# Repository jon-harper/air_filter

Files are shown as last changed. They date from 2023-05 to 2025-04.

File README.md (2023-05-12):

# SUAFT: Still Unnamed Air Filter Thing

3D printer air filtration with HEPA and activated carbon.

## Overview

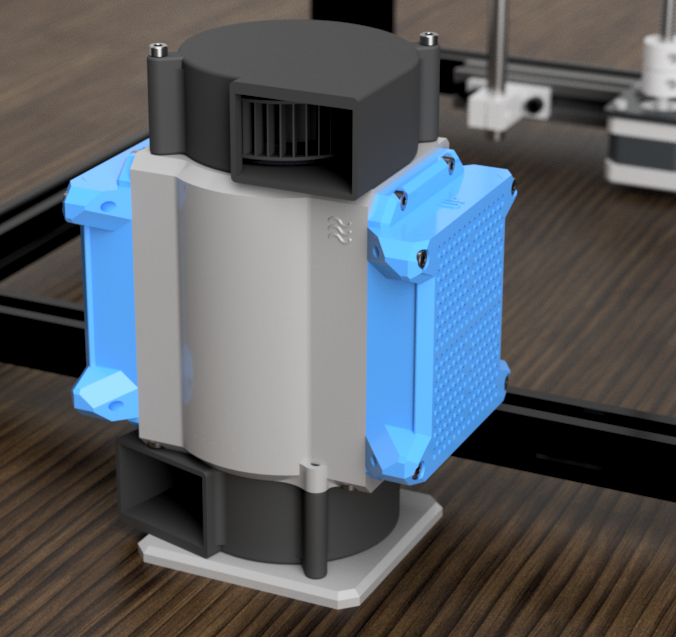
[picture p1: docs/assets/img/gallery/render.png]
render


This is a combination activated carbon and HEPA filter for 3D printing. It uses 75x30mm fans (either one or two) to draw air through a wall of activated carbon pellets and then through a HEPA filter.

The filter can be printed with one fan for filtration only, or with a second fan to provide chamber exhaust or additional airflow.

A method of mounting the filter to 2020 extrusions is coming soon.

[Documentation](https://jon-harper.github.io/air_filter/) is available.

## Bill of Materials
* [Single Filter](https://jon-harper.github.io/air_filter/single/)
* [Dual Filter](https://jon-harper.github.io/air_filter/dual/)

## Assembly
* [Heat Set Insert Locations](https://jon-harper.github.io/air_filter/inserts/)
* [Assembly Guide](https://jon-harper.github.io/air_filter/assembly/)

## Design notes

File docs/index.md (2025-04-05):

---
title: Still Unnamed Air Filter Thing
summary: Landing page for the Still Unnamed Air Filter Thing
authors: Jon Harper
date: 2024-7-31
hide: toc
---

# [SUAFT 120](v3/index.md)

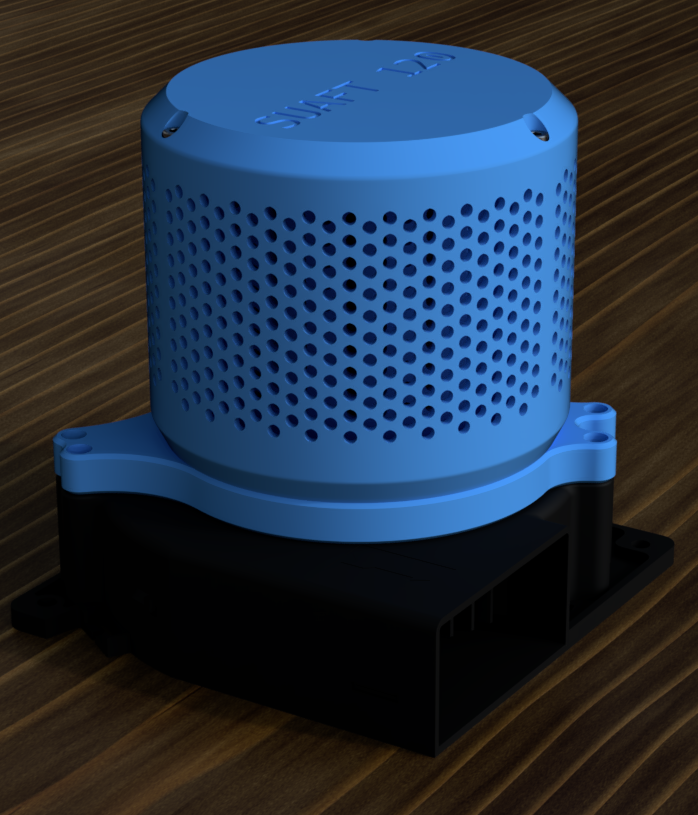
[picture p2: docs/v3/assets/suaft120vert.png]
SUAFT 120


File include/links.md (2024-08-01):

[bom_7530_fan]: https://www.amazon.com/dp/B08NCMY3H5
[bom_hepa]: https://www.amazon.com/gp/product/B08JPDWQCL
[bom_inserts]: https://www.amazon.com/uxcell-Knurled-Insert-Female-Embedding/dp/B09MCWTBCC
[bom_tubing]: https://www.amazon.com/DMiotech-Silicone-Translucent-Industrial-Tubing/dp/B0B59F8WCW
[bom_carbon]: https://www.amazon.com/dp/B00XIIDB8Y/
[bom_magnet]: https://www.amazon.com/TRYMAG-Magnets-Refrigerator-Whiteboard-Neodymium/dp/B09QHSB2XM/

[stl_main_body]:  https://github.com/jon-harper/air_filter/blob/main/STL/V1/main_body.stl
[stl_exhaust_coupler]: https://github.com/jon-harper/air_filter/blob/main/STL/V1/exhaust_coupler.stl
[stl_fan_base]:   https://github.com/jon-harper/air_filter/blob/main/STL/V1/fan_base.stl
[stl_fan_cap]:    https://github.com/jon-harper/air_filter/blob/main/STL/V1/fan_cap.stl
[stl_simple_cap]: https://github.com/jon-harper/air_filter/blob/main/STL/V1/simple_cap.stl
[stl_filter_base]:    https://github.com/jon-harper/air_filter/blob/main/STL/V1/ac_filter/filter_base.stl
[stl_filter_cover]:   https://github.com/jon-harper/air_filter/blob/main/STL/V1/ac_filter/filter_cover.stl
[stl_cpap_coupler]: https://github.com/jon-harper/air_filter/blob/main/STL/V1/15mm_cpap_coupler.stl

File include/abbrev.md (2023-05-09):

*[SHCS]: socket head cap screw
*[AC]: activated carbon
*[HEPA]: high efficiency particulate air

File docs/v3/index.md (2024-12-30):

---
title: SUAFT 120 Introduction
summary: Overview of the 120mm version of SUAFT.
authors: Jon Harper
date: 2024-12-8
hide: toc
---

<div markdown class="jh-grid-container jh-grid-2">
<div markdown class="jh-card">

SUAFT 120 is an activated carbon and HEPA filter for 3D printer enclosures. SUAFTs are designed to be simple, cheap, and efficient; v3 builds on v1 with a sleeker design and easier disassembly.

## Goals

1. Be simple and efficient.
2. Be easy to build.
3. Be cheap to source.
</div>
<div markdown class="jh-grid-img">
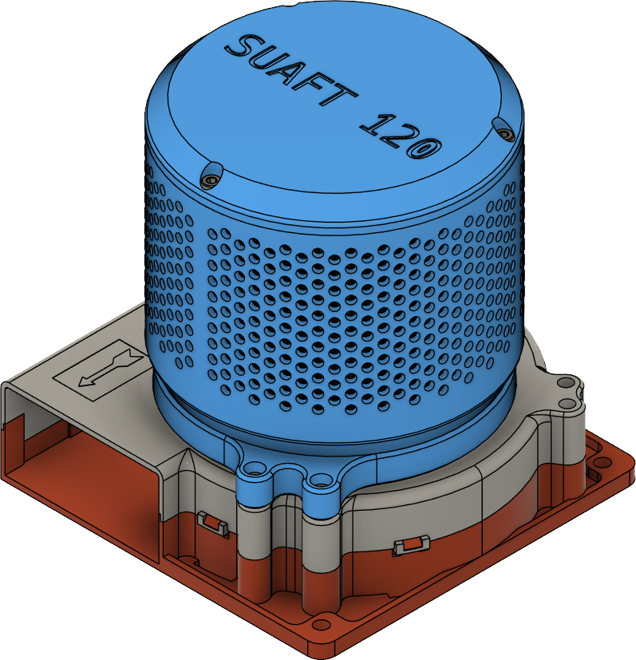
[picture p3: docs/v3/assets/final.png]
SUAFT

</div>
</div>

## Bill of Materials

The filter can be printed for single or dual fan operation. A single fan should be used for continuous filtration. Dual fans can be used for large format printers or as an exhaust filter.

[SUAFT 120 Bill of Materials](bom.md){ .md-button }

## Materials

Material choice is guided by enclosure operating temperature.

- CF-ASA, CF-ABS: >80C, <95C
- ASA: >60C
- ABS: >45C. Avoid with active heaters.
- PETG: <45C or chamber floor. PETG filters should be considered a temporary solution (expected to fail with time). Do not use with active heaters.

## Assembly
 
[Preparation](prep.md){ .md-button }

[Assembly](assembly.md){ .md-button }

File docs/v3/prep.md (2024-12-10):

---
title: Preparation
summary: Simple assembly overview
authors: Jon Harper
date: 2024-12-8
---

## Heat Set Inserts

<figure markdown>
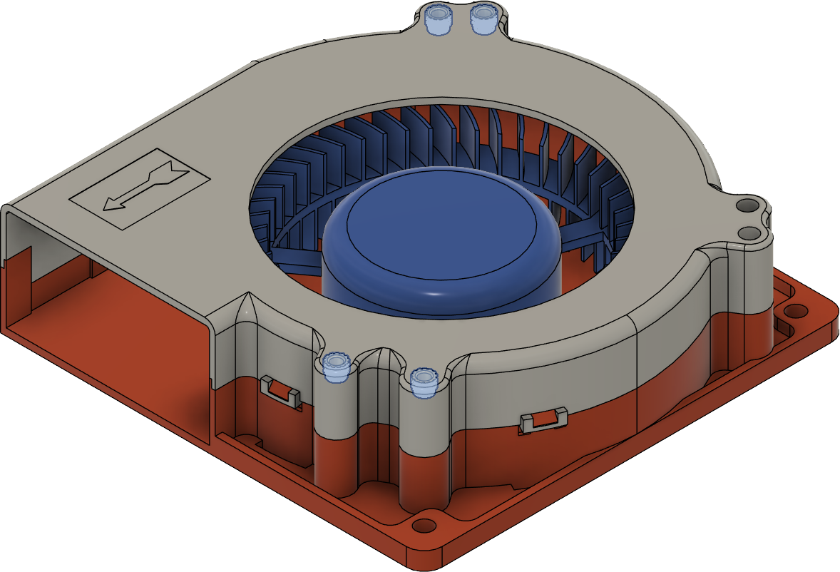
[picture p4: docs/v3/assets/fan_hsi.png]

<figcaption markdown>
Step 1. Install heat set inserts into three (3) of the four (4) highlighted holes in the fan. The fourth may be left unused.
</figcaption>
</figure>

<figure markdown>
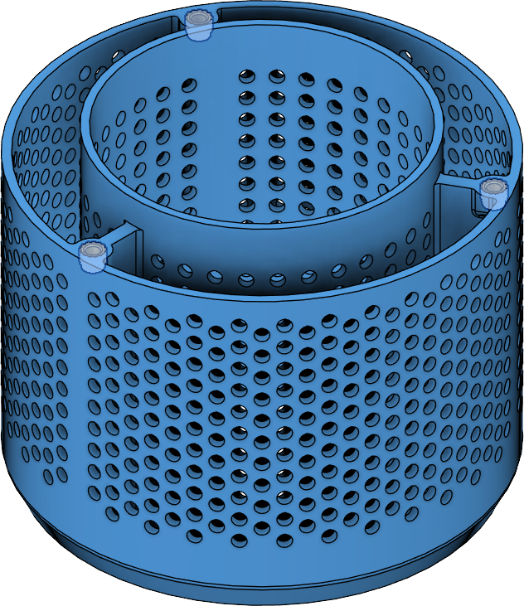
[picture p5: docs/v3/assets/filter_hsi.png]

<figcaption markdown>
Step 2. Install heat set inserts into the three (3) highlighted holes in the fitler cage.
</figcaption>
</figure>

## Magnet Installation

<figure markdown>
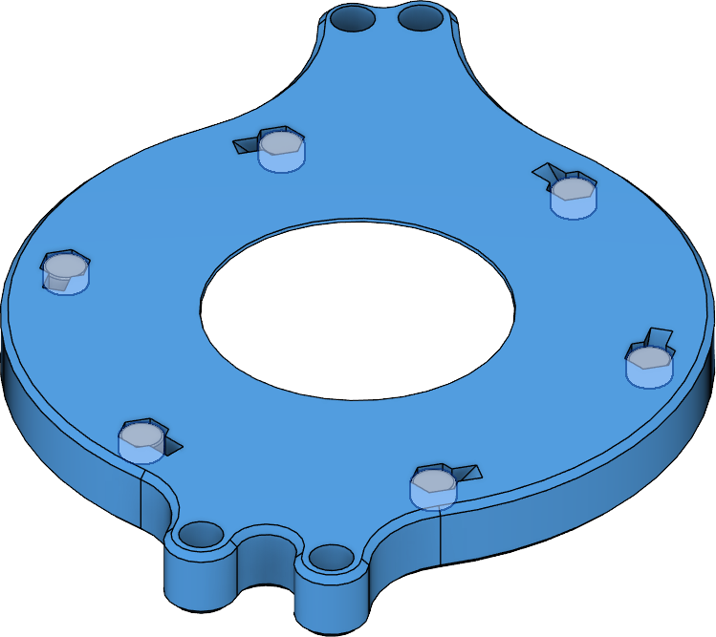
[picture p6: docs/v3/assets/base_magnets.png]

<figcaption markdown>
Step 1. Fix magnets into the six (6) highlighted locations. **It is strongly recommended that the polarity of the magnets are all oriented the same direction.**
</figcaption>
</figure>

<figure markdown>
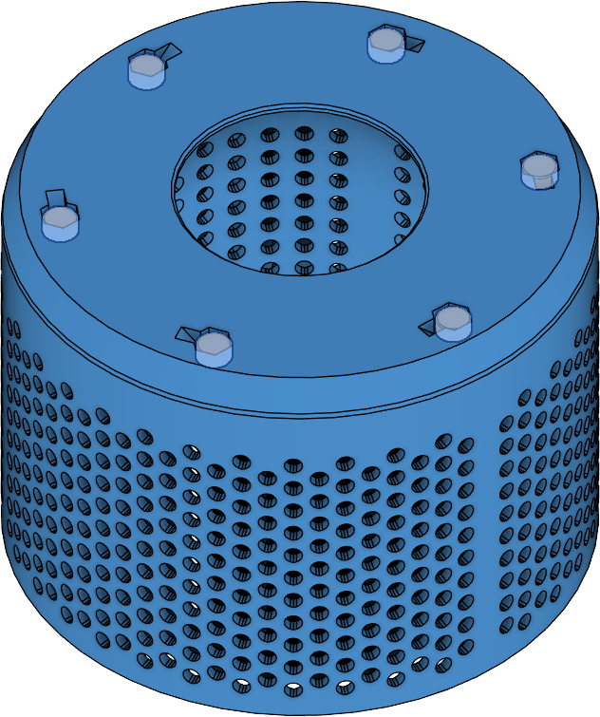
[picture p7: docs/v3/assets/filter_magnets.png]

<figcaption markdown>
Step 2. Fix magnets into the six (6) highlighted locations. **These magnets must have the same orientation as the base magnets.**
</figcaption>
</figure>

<figure markdown>
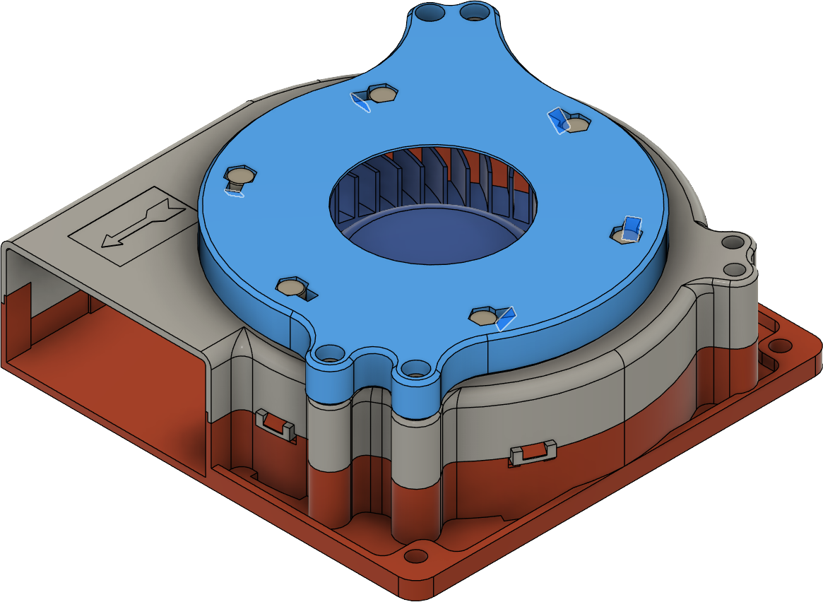
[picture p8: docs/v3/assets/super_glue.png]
step 3

<figcaption markdown>
Step 3. Test that the filter and base snap together properly. Once any issues are fixed, optionally add a drop of super glue to the highlighted well area next to each magnet; this will help ensure magnets do not come loose.
</figcaption>
</figure>

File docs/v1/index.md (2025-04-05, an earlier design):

---
title: v1 Introduction
summary: Landing page for the Still Unnamed Air Filter Thing
authors: Jon Harper
date: 2023-5-5
hide: toc
---

!!! caution
    This project is deprecated. Visit [SUAFT 120](../v3) for the latest design.

<div markdown class="jh-grid-container jh-grid-2">
<div markdown class="jh-card">

SUAFT is an activated carbon and HEPA filter for 3D printer enclosures.

## Goals

1. Be simple and efficient.
2. Be easy to build.
3. Be cheap to source.
</div>
<div markdown class="jh-grid-img">
SUAFT
</div>
</div>
## Bill of Materials

The filter can be printed with either one or two fans. The second fan can be used to provide additional airflow or act as a controlled chamber exhaust fan.

A method of mounting the filter to 2020 extrusions is coming soon.

[Single Fan BOM](single.md){ .md-button }

[Dual Fan BOM](dual.md){ .md-button }

## Assembly

Print SUAFT with ASA, ABS, or PETG. If your enclosure regularly reaches 60C, ASA is recommended.

[Heat Set Insert Locations](inserts.md){ .md-button }

[Assembly Guide](assembly.md){ .md-button }

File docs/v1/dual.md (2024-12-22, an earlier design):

---
title: Dual Fan BOM
summary: Information on the dual fan variation.
authors: Jon Harper
date: 2023-5-7
hide: toc
---

## Materials

| Part | Qty |
|---|-----|
| [Radial 75mm x 30mm fan][bom_7530_fan] | 2 ea |
| [Moosoo XL-618A HEPA Filter][bom_hepa] | 1 ea |
| M3 x 35mm SHCS | 4 ea |
| M3 x 6mm SHCS | 20 ea |
| [Heat set inserts, M3 x 5mm x 4mm][bom_inserts] | 24 ea |
| [Acid-free coconut shell activated carbon][bom_carbon] | < 0.5kg/1lb |
| :material-printer-3d-nozzle: [`main_body.stl`][stl_main_body] | 1 ea |
| :material-printer-3d-nozzle: [`fan_cap.stl`][stl_fan_cap] | 1 ea |
| :material-printer-3d-nozzle: [`fan_base.stl`][stl_fan_base] | 1 ea |
| :material-printer-3d-nozzle: [`filter_base.stl`][stl_filter_base] | 2 ea |
| :material-printer-3d-nozzle: [`filter_cover.stl`][stl_filter_cover] | 2 ea |

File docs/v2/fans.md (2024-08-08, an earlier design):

---
title: 2. Fan Cage(s)
summary: Assembling fan cages
authors: Jon Harper
date: 2024-7-31
---

## Left Fan Cage

<figure markdown>
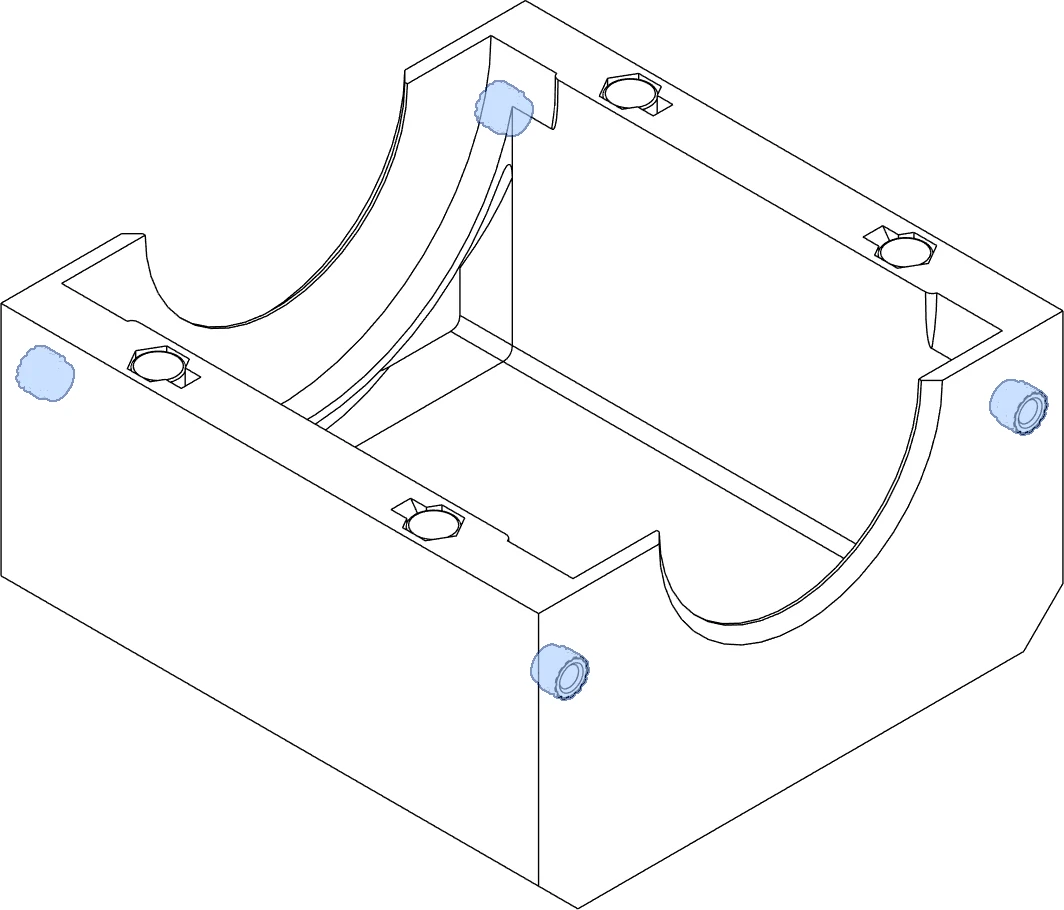
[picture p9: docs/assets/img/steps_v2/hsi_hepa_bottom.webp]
step 1

<figcaption markdown>
Step 1. 
</figcaption>
</figure>

## Right Fan Cage

!!! note
    If your build does not use a second fan, jump to the next section.

<figure markdown>
step 1
<figcaption markdown>
Step 1. 
</figcaption>
</figure>

## Filter Cap

!!! note
    If your build has two (2) fans, skip this section.

<figure markdown>
step 1
<figcaption markdown>
Step 1. 
</figcaption>
</figure>

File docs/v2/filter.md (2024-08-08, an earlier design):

---
title: 3. Filter Assembly
summary: Assembling the filter
authors: Jon Harper
date: 2024-7-31
---

## AC Filter

## HEPA Filter

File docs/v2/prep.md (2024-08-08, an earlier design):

---
title: 1. Prep
summary: Simple assembly overview
authors: Jon Harper
date: 2024-7-31
---

## Heat Set Inserts

<figure markdown>
step 1
<figcaption markdown>
Step 1. 
</figcaption>
</figure>

<figure markdown>
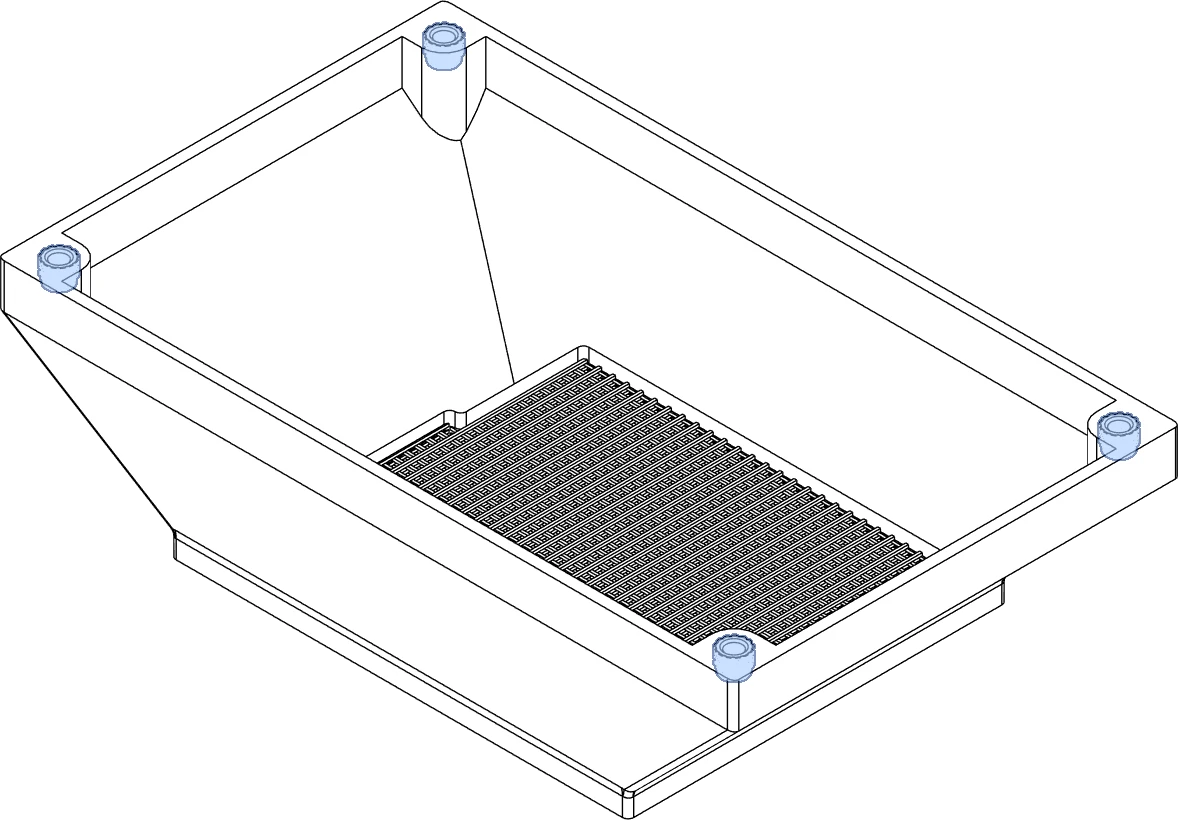
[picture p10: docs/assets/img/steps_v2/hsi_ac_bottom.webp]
step 2

<figcaption markdown>
Step 2. 
</figcaption>
</figure>

<figure markdown>
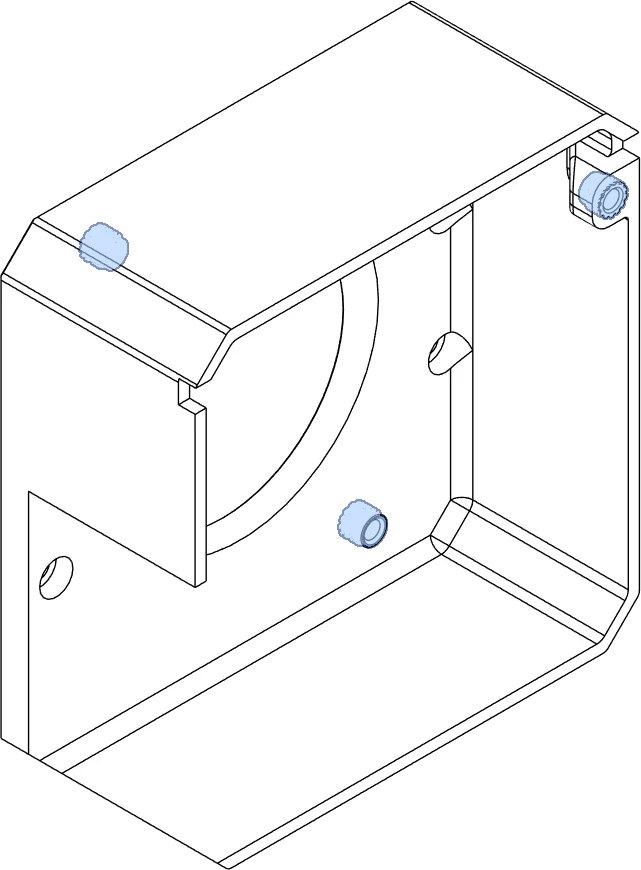
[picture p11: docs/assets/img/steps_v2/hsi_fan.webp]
step 3

<figcaption markdown>
Step 3. 
</figcaption>
</figure>

## Magnet Installation

<figure markdown>
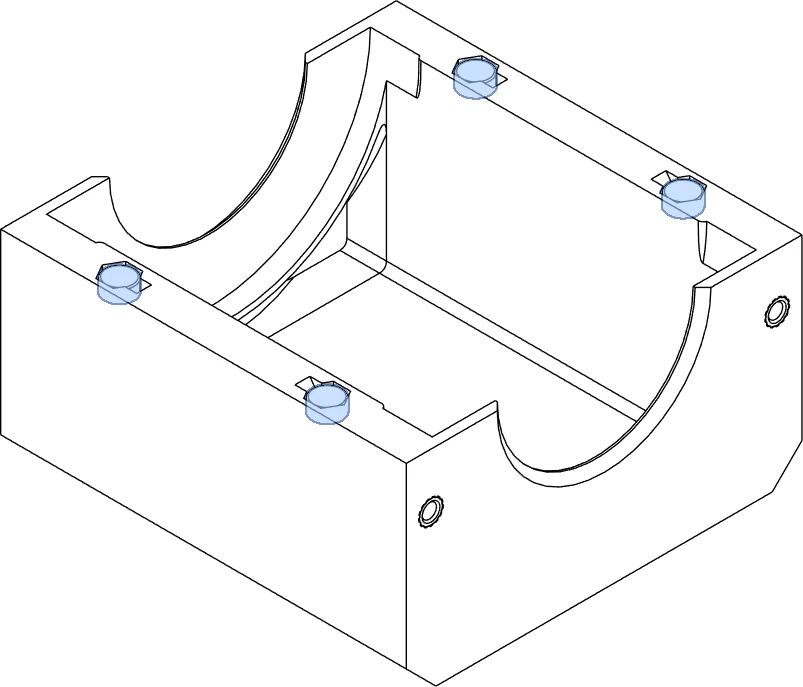
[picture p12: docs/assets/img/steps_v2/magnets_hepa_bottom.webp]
step 1

<figcaption markdown>
Step 1. 
</figcaption>
</figure>

<figure markdown>
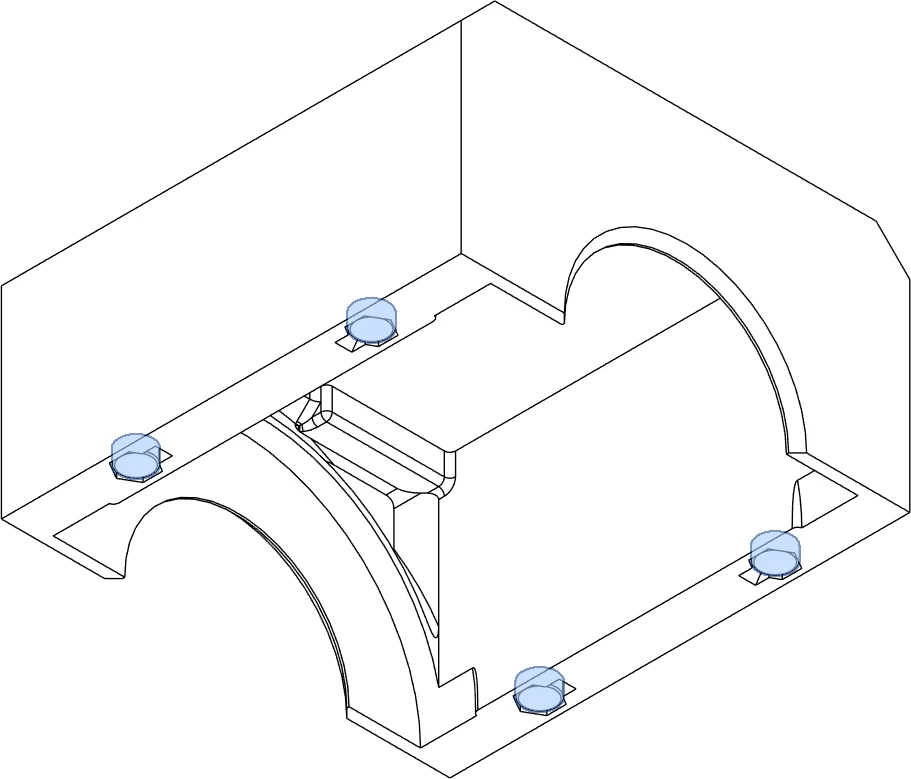
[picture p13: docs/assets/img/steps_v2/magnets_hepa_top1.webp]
step 2

<figcaption markdown>
Step 2. 
</figcaption>
</figure>

<figure markdown>
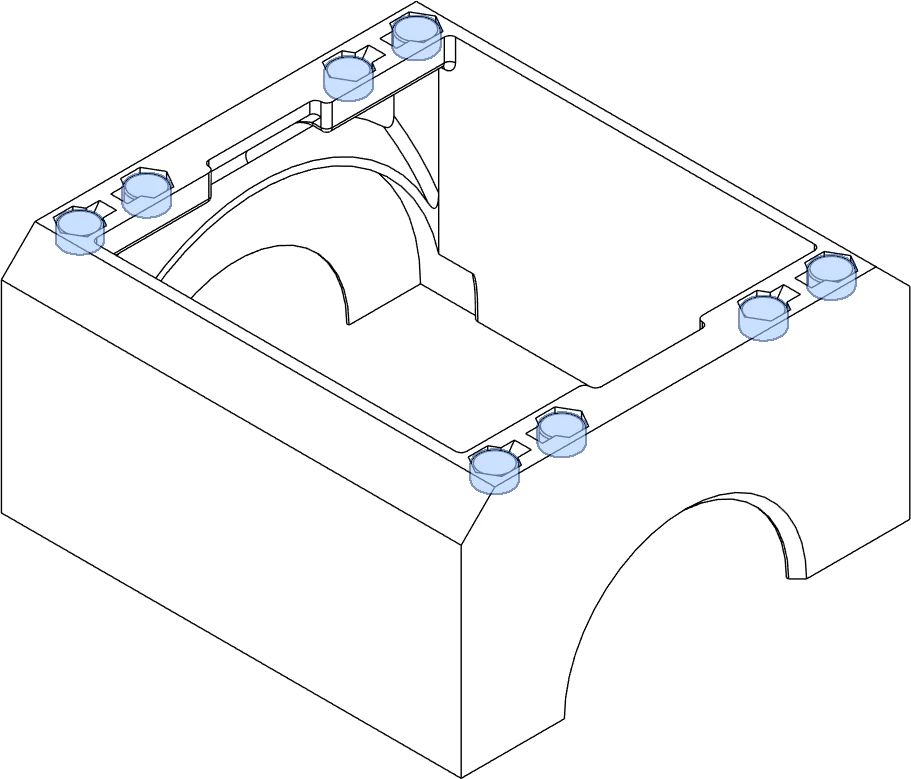
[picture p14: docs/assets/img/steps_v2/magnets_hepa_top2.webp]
step 3

<figcaption markdown>
Step 3. 
</figcaption>
</figure>

<figure markdown>
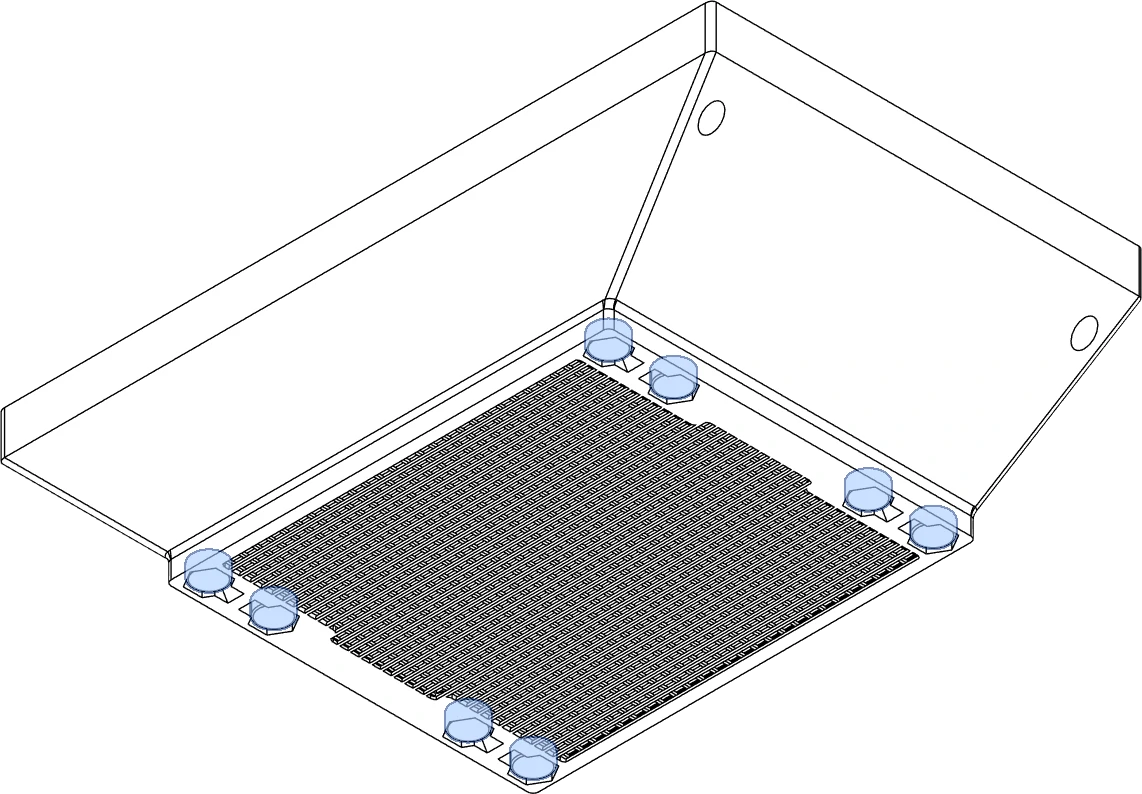
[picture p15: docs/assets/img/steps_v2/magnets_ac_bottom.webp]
step 4

<figcaption markdown>
Step 4. 
</figcaption>
</figure>

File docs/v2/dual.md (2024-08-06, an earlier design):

---
title: Dual Fan BOM
summary: Information on the dual fan variation.
authors: Jon Harper
date: 2024-7-31
hide: toc
---

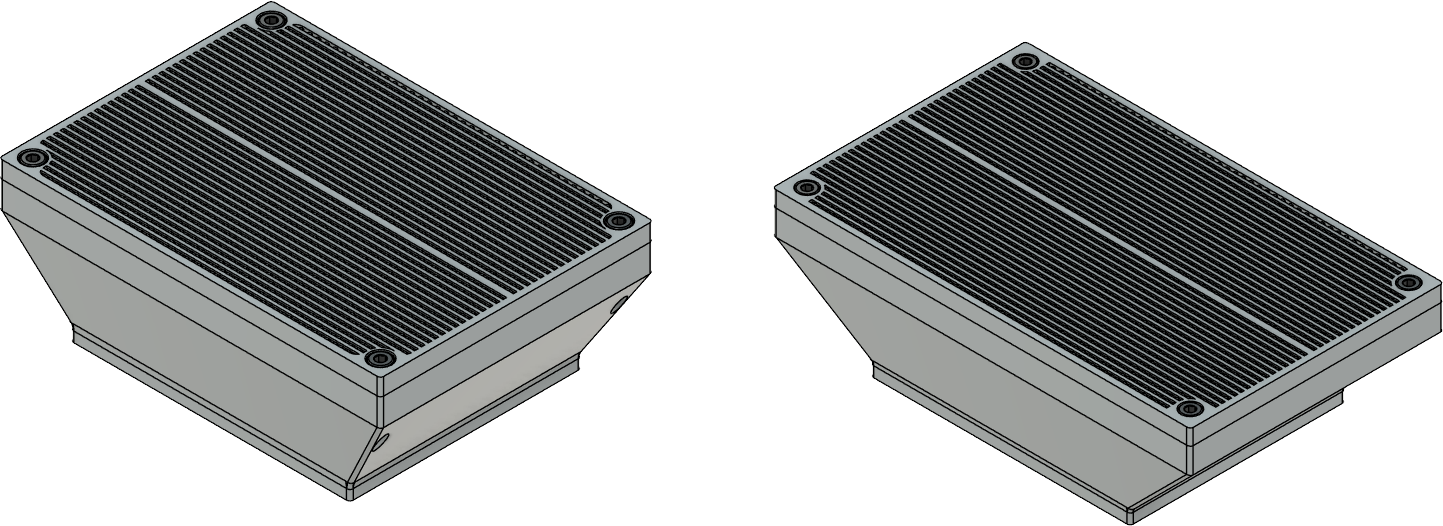
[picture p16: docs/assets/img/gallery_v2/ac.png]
preview


## Materials

| Part | Qty |
|---|-----|
| [Radial 75mm x 30mm fan][bom_7530_fan] | 2 ea |
| [Moosoo XL-618A HEPA Filter][bom_hepa] | 1 ea |
| M3 x 35mm SHCS | 4 ea |
| M3 x 6mm SHCS | 10 ea |
| [6mm x 3mm magnets][bom_magnet] | 24 |
| [Heat set inserts, M3 x 5mm x 4mm][bom_inserts] | 14 ea |
| [Acid-free coconut shell activated carbon][bom_carbon] | < 0.5kg/1lb |
| :material-printer-3d-nozzle: [`HEPA Top.stl`][v2_hepa_top] | 1 ea |
| :material-printer-3d-nozzle: [`HEPA Bottom.stl`][v2_bottom] | 1 ea |
| :material-printer-3d-nozzle: [`Fan Base.stl`][v2_fan_lid] | 2 ea |
| :material-printer-3d-nozzle: [`Fan Lid.stl`][v2_ac_lid_solo] | 2 ea |
| :material-printer-3d-nozzle: [`AC Base - Solo.stl`][v2_ac_base_solo] | 1 ea |
| :material-printer-3d-nozzle: [`AC Lid - Solo.stl`][v2_ac_lid_solo] | 1 ea |

[v2_coupler]: https://github.com/jon-harper/air_filter/blob/main/STL/V2/Fan%20Cages/15mm%20CPAP%20Coupler.stl
[v2_ac_base_duo]: https://github.com/jon-harper/air_filter/blob/main/STL/V2/AC%20Filter/AC%20Base%20-%20Duo.stl
[v2_ac_base_solo]: https://github.com/jon-harper/air_filter/blob/main/STL/V2/AC%20Filter/AC%20Base%20-%20Solo.stl
[v2_ac_lid_duo]: https://github.com/jon-harper/air_filter/blob/main/STL/V2/AC%20Filter/AC%20Lid%20-%20Duo.stl
[v2_ac_lid_solo]: https://github.com/jon-harper/air_filter/blob/main/STL/V2/AC%20Filter/AC%20Lid%20-%20Solo.stl
[v2_fan_base]: https://github.com/jon-harper/air_filter/blob/main/STL/V2/Fan%20Cages/Fan%20Base.stl
[v2_fan_lid]: https://github.com/jon-harper/air_filter/blob/main/STL/V2/Fan%20Cages/Fan%20Lid.stl
[v2_filter_cap]: https://github.com/jon-harper/air_filter/blob/main/STL/V2/Fan%20Cages/Filter%20Cap.stl
[v2_hepa_top]: https://github.com/jon-harper/air_filter/blob/main/STL/V2/HEPA/HEPA%20Top.stl
[v2_bottom]: https://github.com/jon-harper/air_filter/blob/main/STL/V2/HEPA/HEPA%20Bottom.stl
[v2_bottom_wago]: https://github.com/jon-harper/air_filter/blob/main/STL/V2/HEPA/HEPA%20Bottom%20-%20Wagos.stl
[v2_bottom_2020]: https://github.com/jon-harper/air_filter/blob/main/STL/V2/HEPA/HEPA%20Bottom%20-%202020%20Mount.stl
[v2_bottom_2020_splitter]: https://github.com/jon-harper/air_filter/blob/main/STL/V2/HEPA/HEPA%20Bottom%20-%202020%20Mount%20with%20Splitter.stl
[v2_bottom_2020_wago]: https://github.com/jon-harper/air_filter/blob/main/STL/V2/HEPA/HEPA%20Bottom%20-%202020%20Mount%20with%20Wagos.stl

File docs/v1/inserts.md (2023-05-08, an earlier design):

---
title: Heat Set Inserts
summary: Locations of heat set inserts
authors: Jon Harper
date: 2023-5-7
# hide: toc
---

## main_body.stl

<div markdown class="jh-grid-container jh-grid-2">
<div markdown class="jh-grid-img">
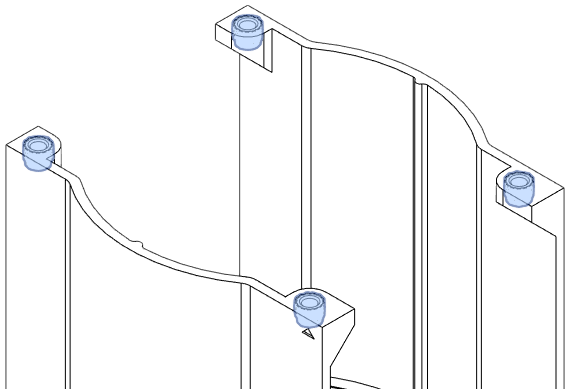
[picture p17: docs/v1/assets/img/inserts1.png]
top inserts

</div>
<div markdown class="jh-grid-img">
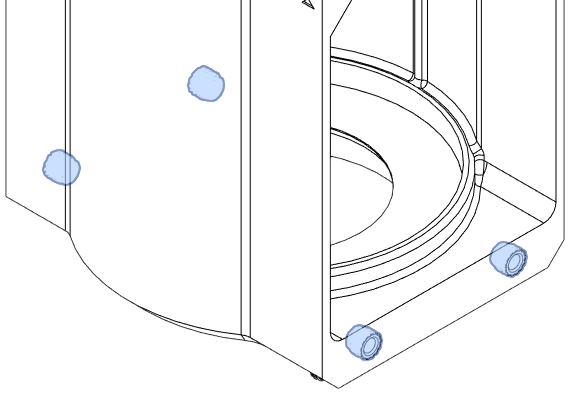
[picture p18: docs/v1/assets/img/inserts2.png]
base inserts

</div>
<div markdown class="jh-grid-img">
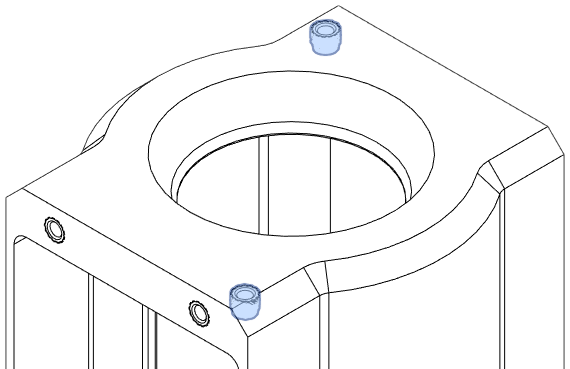
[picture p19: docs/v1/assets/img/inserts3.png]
fan inserts

</div>
</div>

## fan_cap.stl

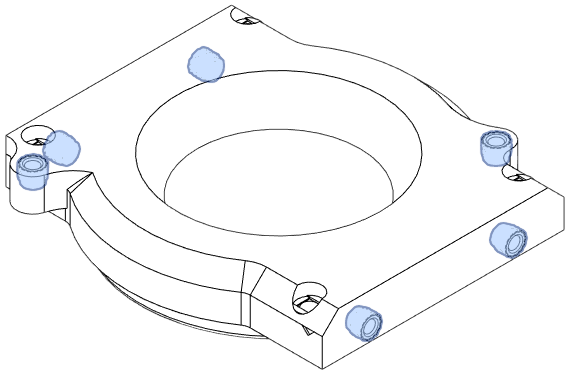
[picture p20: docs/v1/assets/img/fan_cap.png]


## filter_base.stl

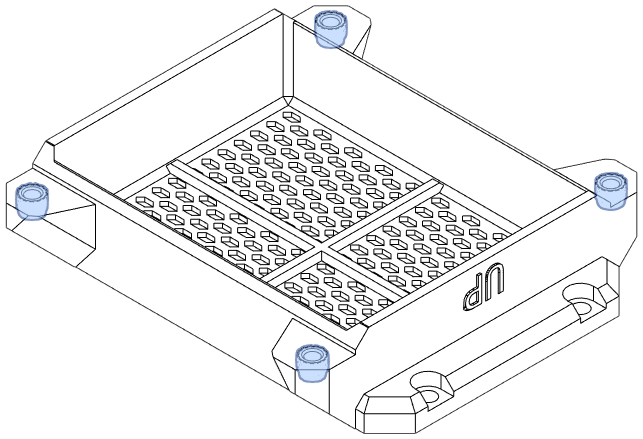
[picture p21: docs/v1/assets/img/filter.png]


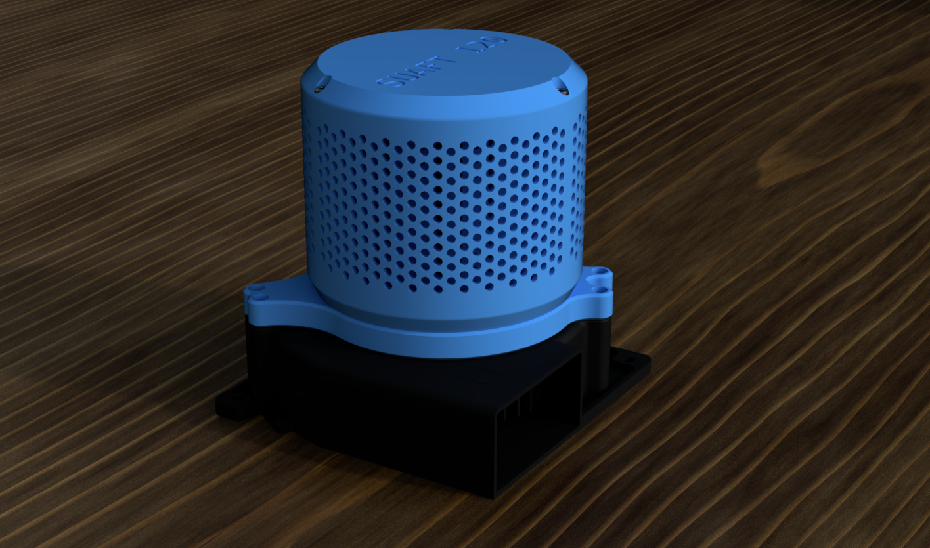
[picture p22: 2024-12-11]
docs/v3/assets/suaft120.png

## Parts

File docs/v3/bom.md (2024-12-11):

---
title: Bill of Materials
summary: Information on the dual fan variation.
authors: Jon Harper
date: 2024-12-8
hide: toc
---

## Materials

| Part | Qty |
|---|-----|
| [Radial 120mm x 32mm fan][bom_120_fan] | 1 ea |
| [Moosoo XL-618A HEPA Filter][bom_hepa] | 1 ea |
| M3 x 6mm SHCS | 6 ea |
| [6mm x 3mm magnets][bom_magnet] | 12 |
| [Heat set inserts, M3 x 5mm x 4mm][bom_inserts] | 6 ea |
| [Acid-free coconut shell activated carbon][bom_carbon] | < 0.5kg/1lb |
| :material-printer-3d-nozzle: [`Base.stl`][120_base] | 1 ea |
| :material-printer-3d-nozzle: [`Filter Cap.stl`][120_filter_cap] | 1 ea |
| :material-printer-3d-nozzle: [`Filter.stl`][120_filter] | 1 ea |
| :material-printer-3d-nozzle: [`Funnel.stl`][120_funnel] | 1 ea, Optional |

[120_base]: https://github.com/jon-harper/air_filter/blob/main/STL/120/Base.stl
[120_filter_cap]: https://github.com/jon-harper/air_filter/blob/main/STL/120/Filter%20Cap.stl
[120_filter]: https://github.com/jon-harper/air_filter/blob/main/STL/120/Filter.stl
[120_funnel]: https://github.com/jon-harper/air_filter/blob/main/STL/120/Funnel.stl
[bom_120_fan]: https://www.amazon.com/Wathai-Brushless-Cooling-Centrifugal-Airflow/dp/B07RMJC9NT/

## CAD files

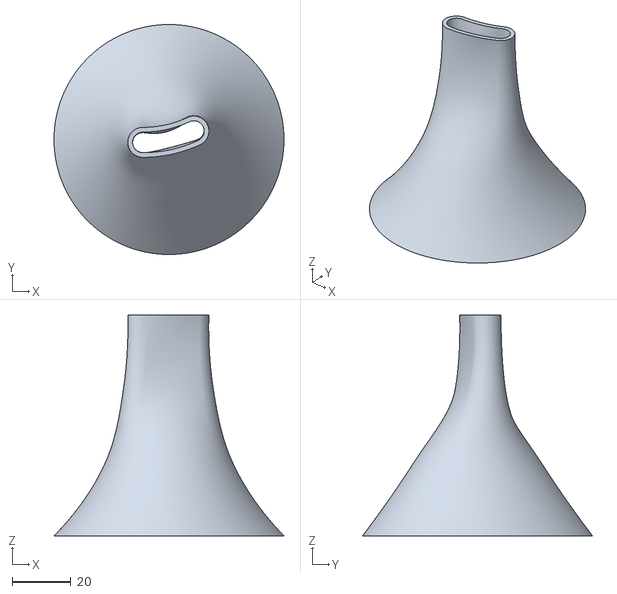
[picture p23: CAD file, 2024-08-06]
STL/120/Funnel.stl
78.2 x 78.2 x 75.0

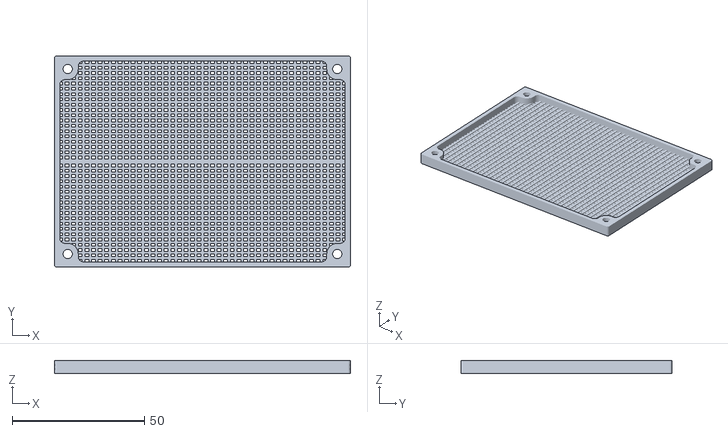
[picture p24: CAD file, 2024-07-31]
STL/V2/AC Filter/AC Lid - Solo.stl
112.0 x 80.0 x 5.00

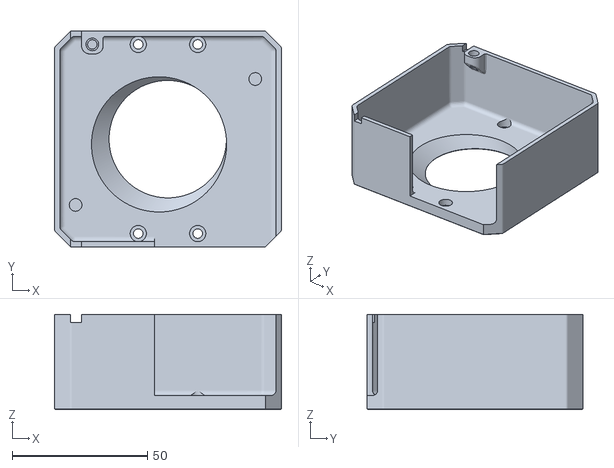
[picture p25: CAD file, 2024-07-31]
STL/V2/Fan Cages/Fan Base.stl
84.0 x 80.0 x 35.2

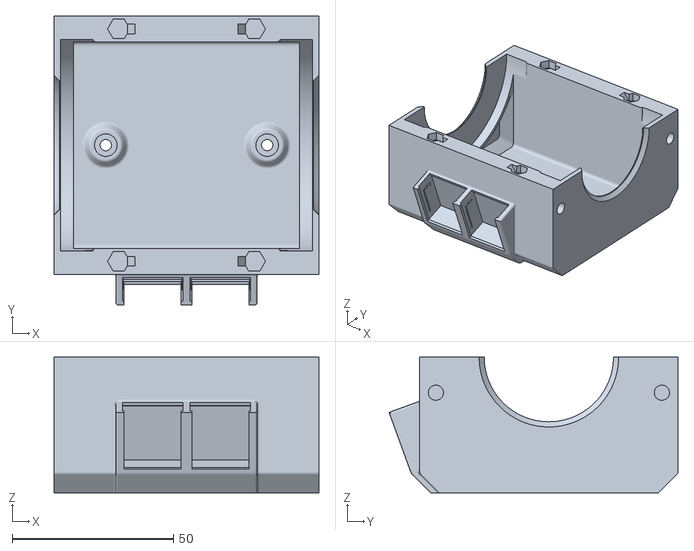
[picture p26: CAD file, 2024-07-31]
STL/V2/HEPA/HEPA Bottom - 2020 Mount with Wagos.stl
82.0 x 89.5 x 42.0

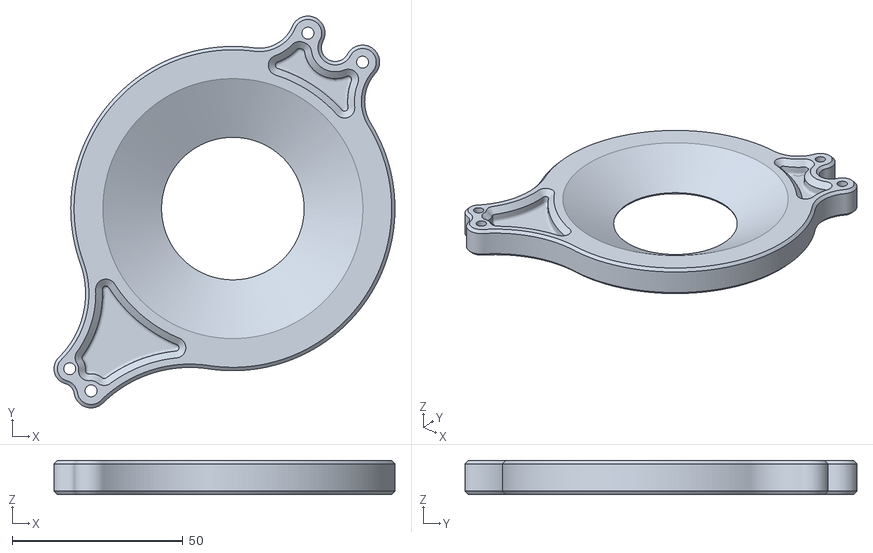
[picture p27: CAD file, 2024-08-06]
STL/120/Base.stl
99.9 x 114.8 x 10.0

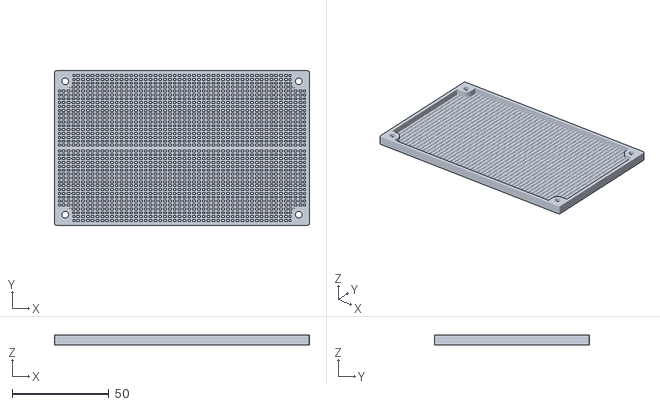
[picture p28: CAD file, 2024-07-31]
STL/V2/AC Filter/AC Lid - Duo.stl
132.0 x 80.0 x 5.00

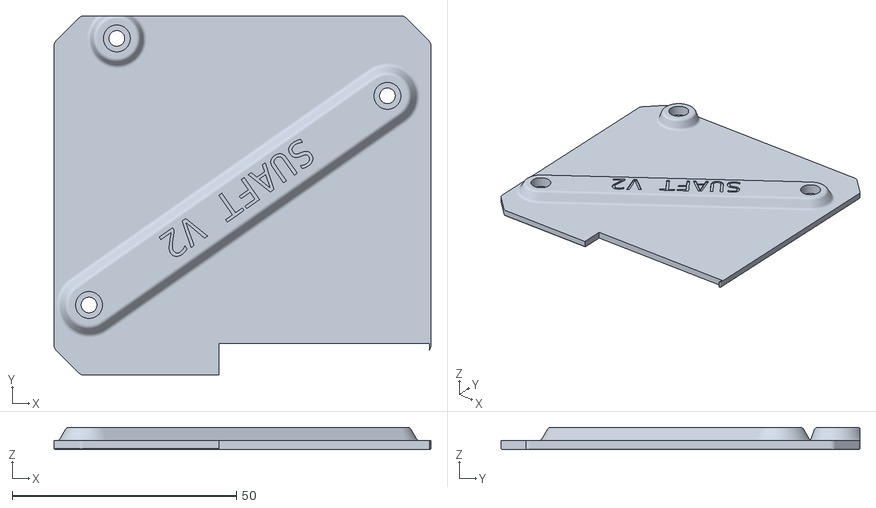
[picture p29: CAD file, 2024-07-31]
STL/V2/Fan Cages/Exhaust Fan Lid.stl
84.0 x 80.0 x 5.00

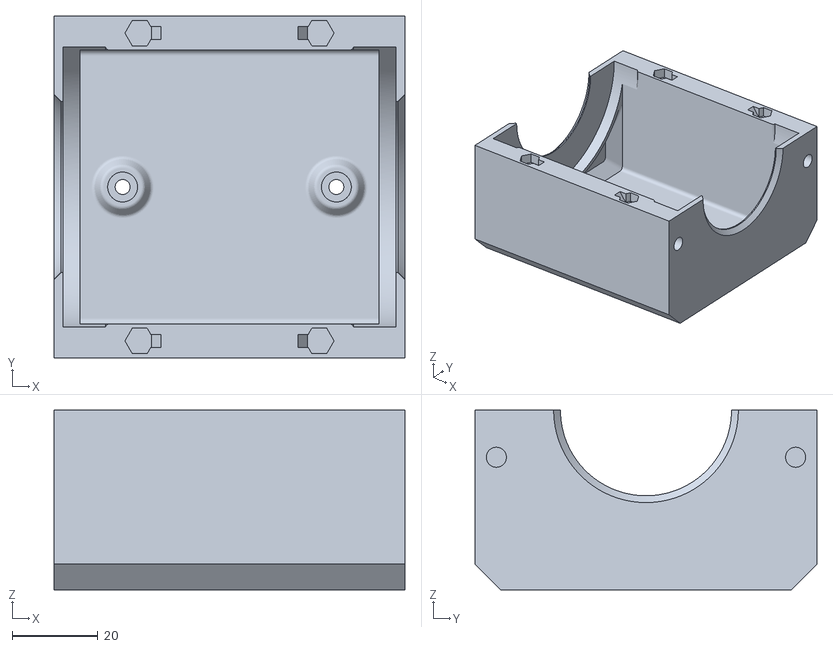
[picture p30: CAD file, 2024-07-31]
STL/V2/HEPA/HEPA Bottom - 2020 Mount.stl
82.0 x 80.0 x 42.0

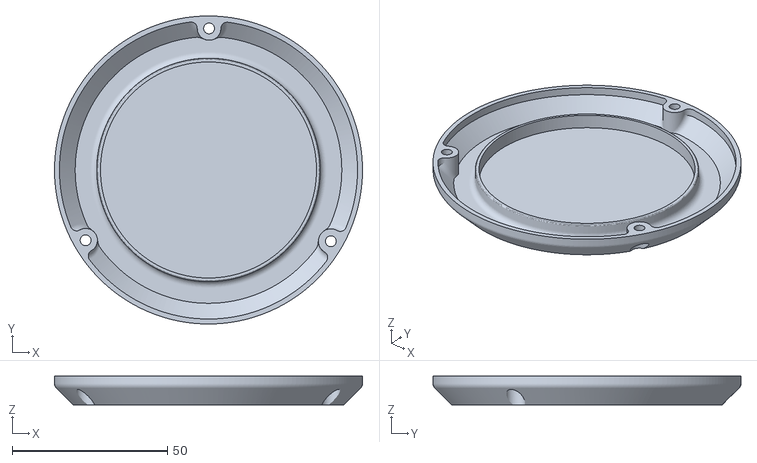
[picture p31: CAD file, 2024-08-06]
STL/120/Filter Cap.stl
99.1 x 99.1 x 9.25

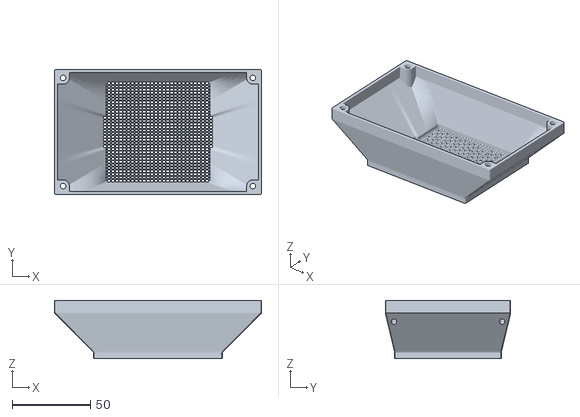
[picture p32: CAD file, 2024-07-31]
STL/V2/AC Filter/AC Base - Duo.stl
132.0 x 80.0 x 37.0

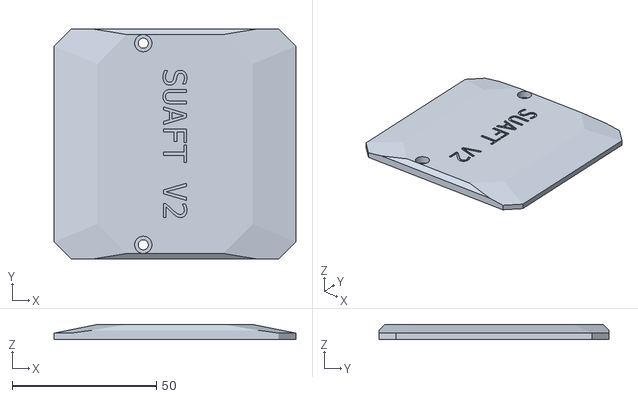
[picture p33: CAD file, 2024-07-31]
STL/V2/Fan Cages/Filter Cap.stl
84.0 x 80.0 x 5.20

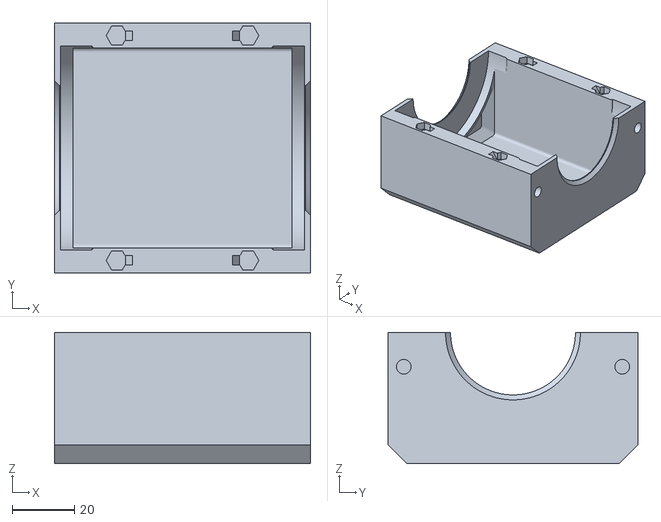
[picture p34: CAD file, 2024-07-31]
STL/V2/HEPA/HEPA Bottom.stl
82.0 x 80.0 x 42.0

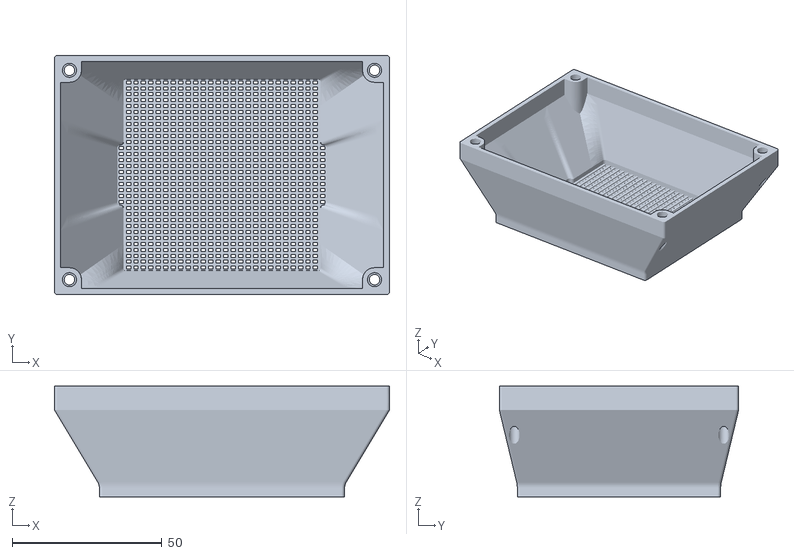
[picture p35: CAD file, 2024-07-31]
STL/V2/AC Filter/AC Base - Solo.stl
112.0 x 80.0 x 37.0

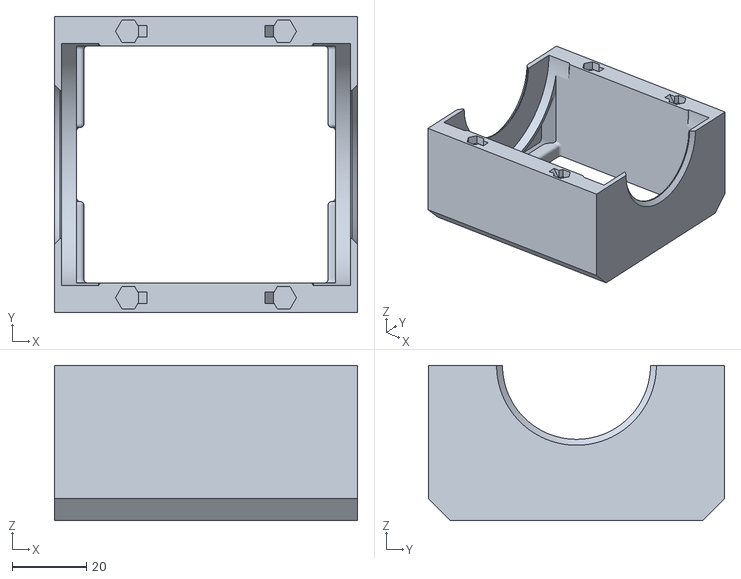
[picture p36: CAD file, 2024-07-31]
STL/V2/HEPA/HEPA Top.stl
82.0 x 80.0 x 42.0

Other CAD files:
STL/V2/Fan Cages/Exhaust Fan Base.stl
STL/V2/Fan Cages/Fan Lid.stl
STL/V2/HEPA/HEPA Bottom - Wagos.stl
STL/V2/Fan Cages/15mm CPAP Coupler.stl
STL/V1/15mm_cpap_coupler.stl
STL/V1/ac_filter/filter_base.stl
STL/V1/ac_filter/filter_cover.stl
STL/V1/exhaust_coupler.stl
STL/V1/fan_base.stl
STL/V1/fan_cap.stl
STL/V1/main_body.stl
STL/V1/simple_cap.stl
STL/V2/HEPA/HEPA Bottom - 2020 Mount with Splitter.stl

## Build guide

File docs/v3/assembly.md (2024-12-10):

---
title: Assembly
summary: Assembling the printed parts, fan, and filter
authors: Jon Harper
date: 2024-12-8
---

<figure markdown>
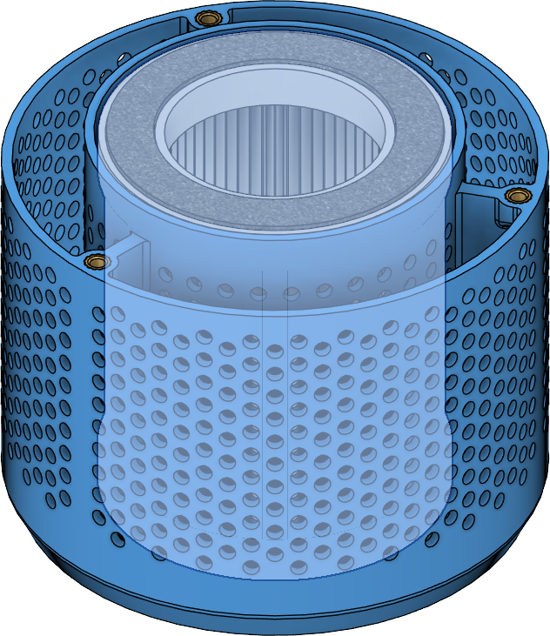
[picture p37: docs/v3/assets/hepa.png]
step 1

<figcaption markdown>
Step 1. Insert a HEPA filter into the center of the filter tank.
</figcaption>
</figure>

<figure markdown>
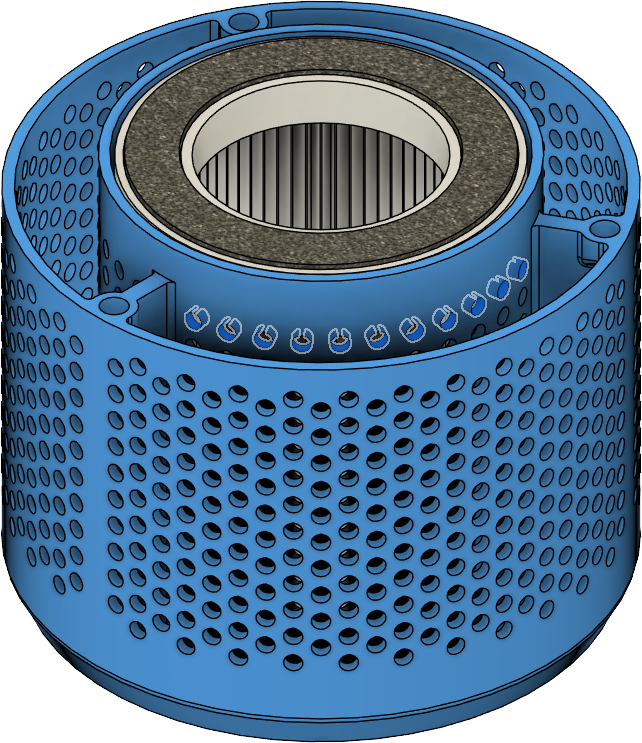
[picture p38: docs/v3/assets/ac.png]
step 2

<figcaption markdown>
Step 2. Use a funnel to add activated carbon to the outer tank. Fill until the carbon covers the highlighted holes in the tank.
</figcaption>
</figure>

<figure markdown>
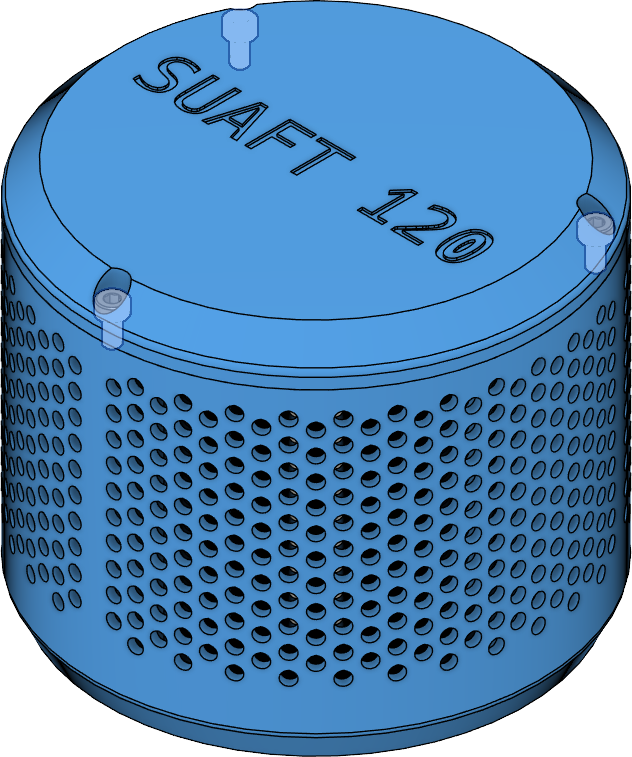
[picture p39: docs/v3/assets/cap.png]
step 3

<figcaption markdown>
Step 3. Cover the filter tank with the lid. Secure with three (3) M3 x 6mm screws.
</figcaption>
</figure>

<figure markdown>
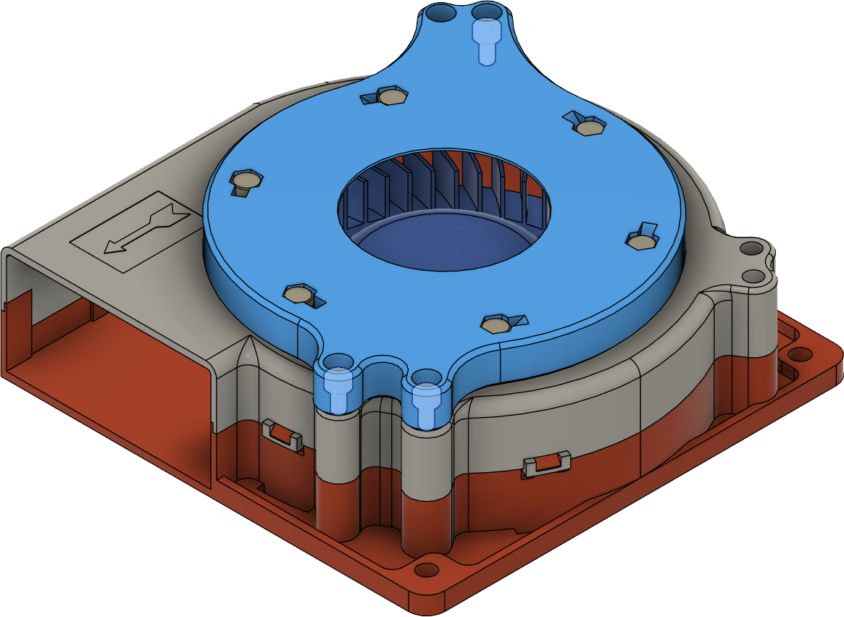
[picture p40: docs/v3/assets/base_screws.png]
step 4

<figcaption markdown>
Step 4. Attach the base to the 120mm fan with **three (3)** M3 x 6mm screws.
</figcaption>
</figure>

<figure markdown>
step 5
<figcaption markdown>
Step 5. Snap the filter and base together. Your SUAFT 120 is now ready!
</figcaption>
</figure>

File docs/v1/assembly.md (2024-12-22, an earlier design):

---
title: Assembly Guide
summary: Simple assembly overview
authors: Jon Harper
date: 2023-5-9
---

## Activated Carbon Filter

<figure markdown>
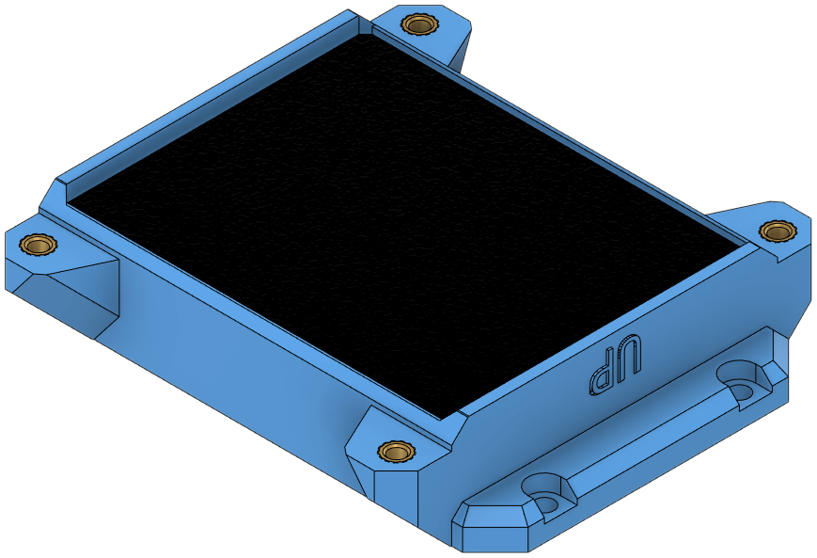
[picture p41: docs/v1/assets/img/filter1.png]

<figcaption markdown>
Step 1. Fill the filter with activated carbon until nearly overflowing.
</figcaption>
</figure>

<figure markdown>
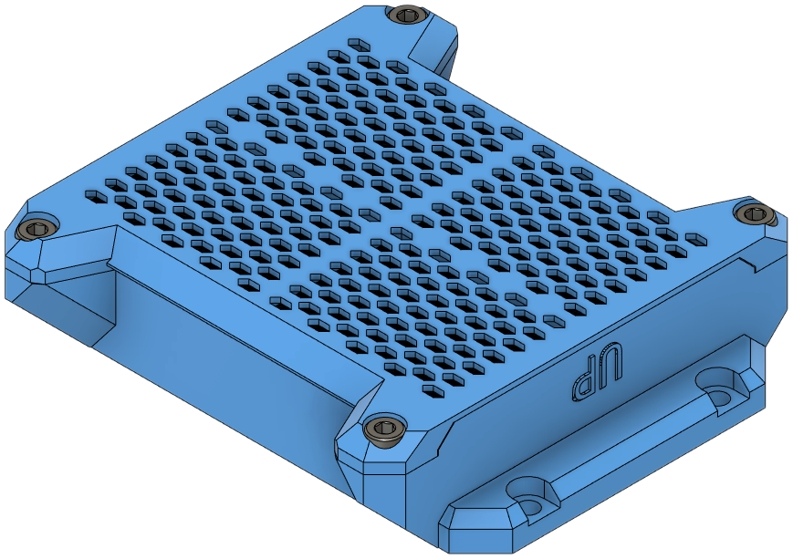
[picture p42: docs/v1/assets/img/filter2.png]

<figcaption markdown>
Step 2. Place the cover over the filter. Secure with four (4) M3 x 6mm SHCS.
</figcaption>
</figure>

## Filter Body

<figure markdown>
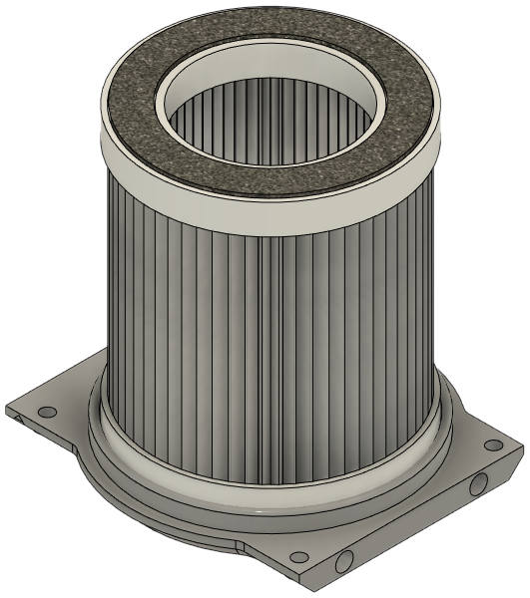
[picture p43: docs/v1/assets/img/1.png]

<figcaption markdown>
Step 1. Fit the HEPA filter on to the cap. It should be a snug fit.
</figcaption>
</figure>

<figure markdown>
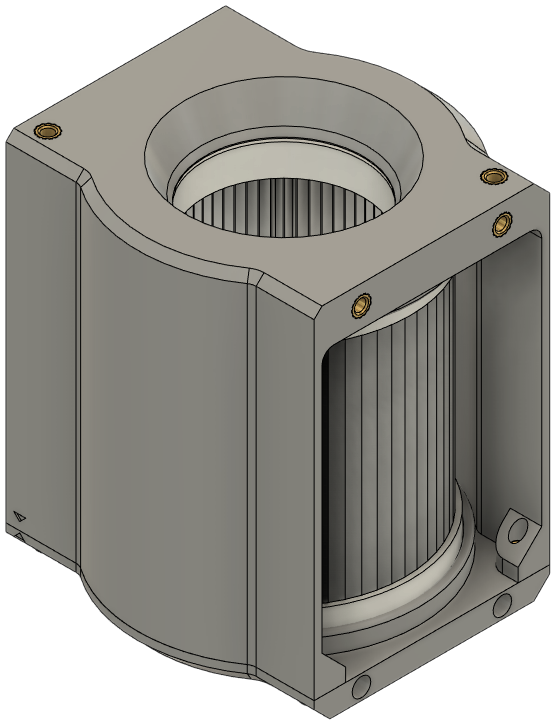
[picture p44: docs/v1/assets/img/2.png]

<figcaption markdown>
Step 2. Note the arrow in the bottom left corner. Align the arrows on the cap and main body while pressing them together. 
</figcaption>
</figure>

<figure markdown>
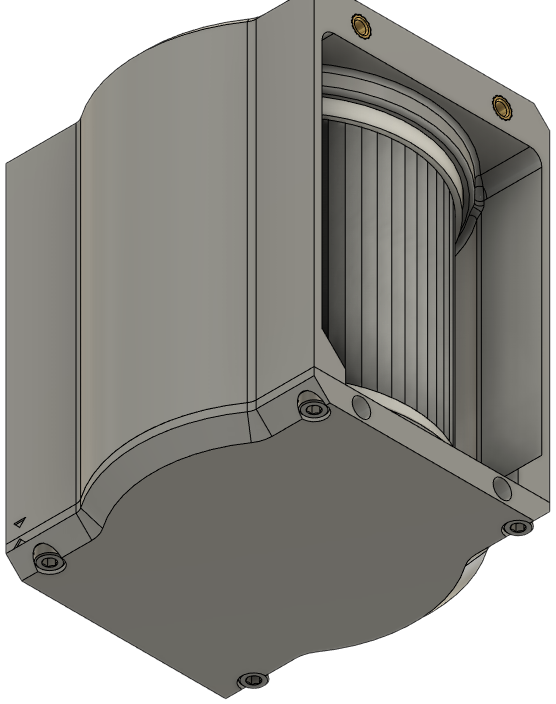
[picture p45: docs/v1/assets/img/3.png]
step 3

<figcaption markdown>
Step 3. Secure the cap and main body with four (4) M3 x 6mm SHCS.
</figcaption>
</figure>

<figure markdown>
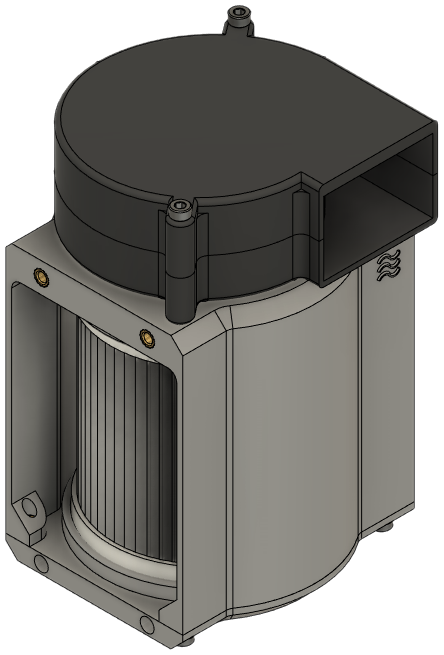
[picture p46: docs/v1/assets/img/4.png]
step 4

<figcaption markdown>
Step 4. Place your radial fan over the fan inlet. The airflow symbol should be directly under the fan. Secure with two (2) M3 x 35mm SHCS.
</figcaption>
</figure>

<figure markdown>
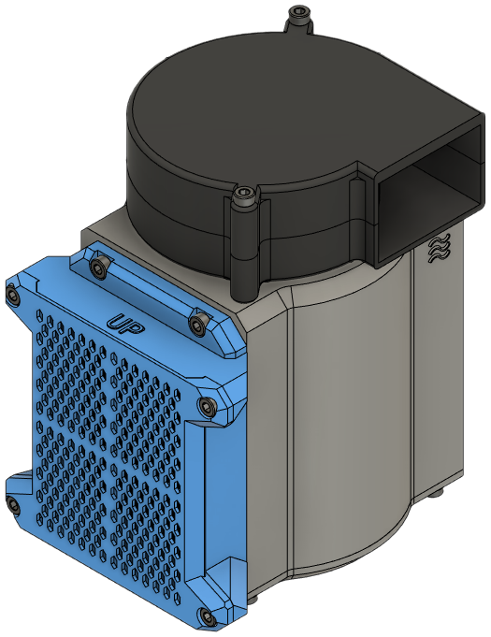
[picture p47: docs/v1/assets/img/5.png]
step 5

<figcaption markdown>
Step 5. Secure a filter to one side with four (4) M3 x 6mm SHCS.
</figcaption>
</figure>

<figure markdown>
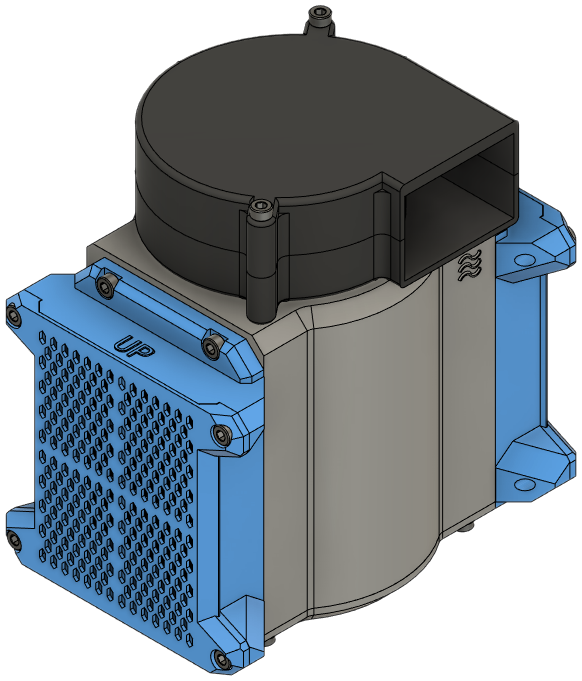
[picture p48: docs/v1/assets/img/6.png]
step 6

<figcaption markdown>
Step 6. Repeat with the second filter and four (4) more M3 x 6mm SHCS.
</figcaption>
</figure>

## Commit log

2023-05-05 Added BOM
2023-05-05 bom links
2023-05-06 Made room for an exhaust coupler
    [main_body.stl]
2023-05-06 Insert location graphics
2023-05-06 Added an exhaust coupler
    [exhaust_coupler.stl]
2023-05-09 Remove interior ribbing
    [main_body.stl]
2023-05-09 Added airflow hint
    [main_body.stl]
2023-05-09 Added assembly steps
2023-05-09 touched up BOM
2023-05-09 Added AC to BOM
2023-05-12 Fixed export
    [main_body.stl]
2023-07-12 Tweaked HEPA clearances
    [fan_cap.stl, main_body.stl, simple_cap.stl]
2023-09-25 Added CAD file
2024-04-16 Initial V2 commit
    [AC Base.stl, AC Lid.stl, Fan Base.stl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]
2024-04-16 File org
    [AC Base - Duo.stl, AC Lid - Duo.stl, HEPA Bottom - Duo.stl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]
2024-04-16 Solo and STEPs
    [AC Base - Solo.stl, AC Lid - Solo.stl, HEPA Bottom - Solo.stl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]
2024-04-20 Moved V1 into subfolder
    [15mm_cpap_coupler.stl, exhaust_coupler.stl, fan_base.stl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]
2024-04-26 Finer filter screens
2024-04-26 Base mesh fix
    [AC Base - Solo.stl]
2024-04-26 New variations
    [HEPA Bottom - Duo - 2020 Mount with Splitter.stl, HEPA Bottom - Duo - 2020 Mount.stl, HEPA Bottom - Solo - 2020 Mount.stl]
2024-04-27 Coarsened filter mesh
    [AC Base - Solo.stl, AC Lid - Solo.stl]
2024-05-01 Wago support
    [HEPA Bottom - Duo - 2020 Mount with Wagos.stl, HEPA Bottom - Duo - Wagos.stl]
2024-05-04 CPAP, print orientation, fixes
    - Added new wiring cutout
    - Added 15mm CPAP coupler
    - Added exhaust version of the fan lid and base
    - Set files in print orientation
    [15mm CPAP Coupler.stl, Exhaust Fan Base.stl, Exhaust Fan Lid.stl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]
2024-07-31 Latest tested iteration
    [15mm CPAP Coupler.stl, AC Base - Duo.stl, AC Base - Solo.stl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]
2024-08-03 reorg; hsi and magnet steps
2024-08-06 split bom pages
2024-08-06 Initial Suaft 120 commit
    [Base.stl, Filter Cap.stl, Funnel.stl]
2024-12-10 fixed landing page
